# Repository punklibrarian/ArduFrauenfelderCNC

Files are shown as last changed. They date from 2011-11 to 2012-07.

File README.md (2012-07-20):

ArduFrauenfelderCNC
=============================
Copyright 2011 Design Tech Industries (DTI)  & Tamworth Hackerspace

DTI email: <the.righteous.avengers@gmail.com> |
THS: <http://tamworthhackerspace.org> |
Google Group: <https://groups.google.com/group/tamworth-hackerspace>

The ArduFrauenfelderCNC is a CNC mill run by an Arduino compatible custom board with 
stepper motor drivers, running grbl.

Board Features:

 * ATmega328 & ATmega32U4 MCU
 * Power LED & Reset switch
 * Populated pins for FTDI breakout board
 * SparkFun EasyDriver v4.4
 * Open Source; OSHW compliant
 * Design files freely available

Mill features:

 * Designed using free tools
 * Simple construction methods
 * Design files freely available

In this repository you will find the gerber files, project (.pro), board (.brd) and schematic (.sch), 
along with a grbl file configured specifically for the board.

**At the moment the files you find here are in the process of development and as such are not 
production ready. It is an ongoing endeavour to create the board and mill satisfactorily. If you can 
help in this regard please contact me, as well as if you find something that needs correction**

**The only files that can be manufactured are those of the ArduFrauenfelderCNC 1.0 - Arduino Pro Micro Edition. 
It should be a fully functional design. As on 20/07/2012 still untested.**

INSIDE THIS REPOSITORY
----------------------
The 'docs' folder within this repository includes a handy copy of the schematic in PNG format and images 
of the pcb/mill, along with assembly documentation.

The 'mill' folder within this repository has design files for the physical mill and documentation 
for it's construction. It has 'sketchup_exported_faces', 'sketchup_models' and 'laser_cutting' folders.
**For license information refer to the attached README.md file in the 'mill' folder**

The 'controller' folder within this repository has all the files needed to create the controller board. 
It has folders for the specific MCU used, 'ATmega328', 'ATmega32U4' (inside these folders are 'EAGLE', 'eagleUp', 
'KiCad' and 'gerbers' folders).

**For license information refer to the attached README.md file in the 'controller' folder**

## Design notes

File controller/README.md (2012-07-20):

ArduFrauenfelderCNC >> Controller Board
=======================================
Copyright 2012 Design Tech Industries (DTI)  & Tamworth Hackerspace

In the 'controller' folder of this repository you can find the design files for the CNC controller board in an ATmega328 
and ATmega32U4 variety. You will find project files in EAGLE and KiCad formats, as well as completed gerber files for the 
board ready to be sent to BatchPCB and OSH Park, which are the the services I designed this board to use, for manufacture.

I have also added eagleUp (http://eagleup.wordpress.com) files as well as a SKP of the resulting conversion 
(minus parts as there aren't any at the moment).

You will also find a customised version of Grbl in the form of a .HEX file. Later versions of the controller 
board will use rStep and be based on the ATmega644p MCU (I am also looking at using an mbed and http://smoothieware.org).

INSTALLATION
------------
**EAGLE**
The design is saved as an EAGLE project. EAGLE PCB design software is available from www.cadsoftusa.com 
free for non-commercial use and can be installed on Windows and Mac, with Linux support through WINE. 
To use this project download it and place the directory containing these files into the "eagle" directory 
on your computer. Then open EAGLE and navigate to Projects -> eagle -> ArduFrauenfelderCNC.

**KiCad**
KiCad EDA Suite is an Open Source alternative to EAGLE. It is available on Windows and Linux and can be installed 
on Mac. It is available from http://kicad.sourceforge.net and works in a similar way to EAGLE. You will find project 
files for KiCad in the aptly named folder in this repository. To use this project download it and place the directory 
containing these files into a folder of your choice. Then open KiCad and navigate to File -> Open -> 
'FOLDER_OF_YOUR_CHOICE' -> ArduFrauenfelderCNC.pro

You will also find a manual in the 'docs' folder for the assembly of the controller board, with colour photos and diagrams. 
**Documentation is separately licensed. See LICENSE section below**

DISTRIBUTION
------------
The specific terms of distribution of this project are governed by the license referenced below.

LICENSE
-------
> CONTROLLER BOARD
> ----------------
> This work is licensed under the Creative Commons Attribution-ShareAlike License.  
> 
> To view a copy of this license, visit:
> 
>   http://creativecommons.org/licenses/by-sa/3.0/  
>   http://creativecommons.org/licenses/by-sa/3.0/legalcode
> 
> or send a letter to
> 
>   Creative Commons  
>   171 Second Street, Suite 300  
>   San Francisco  
>   California, 94105  
>   USA

> DOCUMENTATION
> -------------
> This work is licensed under the GNU Free Documentation License Version 1.3
> 
> To view a copy of this license, visit:
> 
>   http://www.gnu.org/licenses/fdl-1.3.html

The "license" folder within this repository also contains copies of the
license(s) referenced above.

CREDITS
-------
The ArduFrauenfelderCNC was designed by Jamie Johnston (jameskun89@rocketmail.com) 
based on previous work by the Arduino team (www.arduino.cc/playground/Main/People) 
which includes:

 * Massimo Banzi
 * David Cuartielles
 * Tom Igoe
 * Gianluca Martino
 * David A. Mellis

As well as Brian Schmalz, the creator of the EasyDriver Stepper Motor Driver (http://schmalzhaus.com/EasyDriver) 
and Sparkfun, the creator of the Arduino Pro Micro (http://www.sparkfun.com/products/11098).

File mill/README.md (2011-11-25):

ArduFrauenfelderCNC >> Mill
=============================
Copyright 2011 Design Tech Industries (DTI)  & Tamworth Hackerspace

In the 'mill' folder of this repository you will find the design files for the physical mill.
You will be able to use the 3D model of the mill and will be available in either SKP, DXF or STL 
format, most likely all three. You can find the SketchUp models in the 'sketchup_models' folder.

The physical mill is being designed to be manufactured by Ponoko (http://ponoko.com) and as such 
the actual production files for the mill will be made available in SVG and EPS formats. You will 
find the files needed in the 'laser cutting' folder. You will also find the faces exported from 
SketchUp, which are used to create the templates in the 'laser cutting' folder, in the 
'sketchup_exported_faces' folder.

**The SKP, SVG and EPS files currently in this repository are, like the controller board, in 
beta versioning and as such are not ready for actual production. They are merely here for public 
critique, i.e: If you see something wrong, or you think I could be doing something better, then let 
me know.**

You will also find a manual in the 'docs' folder for the assembly of the mill, with colour photos and diagrams. 
**Documentation is separately licensed. See LICENSE section below**

DISTRIBUTION
------------
The specific terms of distribution of this project are governed by the license referenced below.

LICENSE
-------
> MILL
> ----
> This work is licensed under the Creative Commons Attribution-ShareAlike License 3.0  
> 
> To view a copy of this license, visit:
> 
>   http://creativecommons.org/licenses/by-sa/3.0/  
>   http://creativecommons.org/licenses/by-sa/3.0/legalcode
> 
> or send a letter to
> 
>   Creative Commons  
>   171 Second Street, Suite 300  
>   San Francisco  
>   California, 94105  
>   USA

The "license" folder within this repository also contains copies of the
license(s) referenced above.

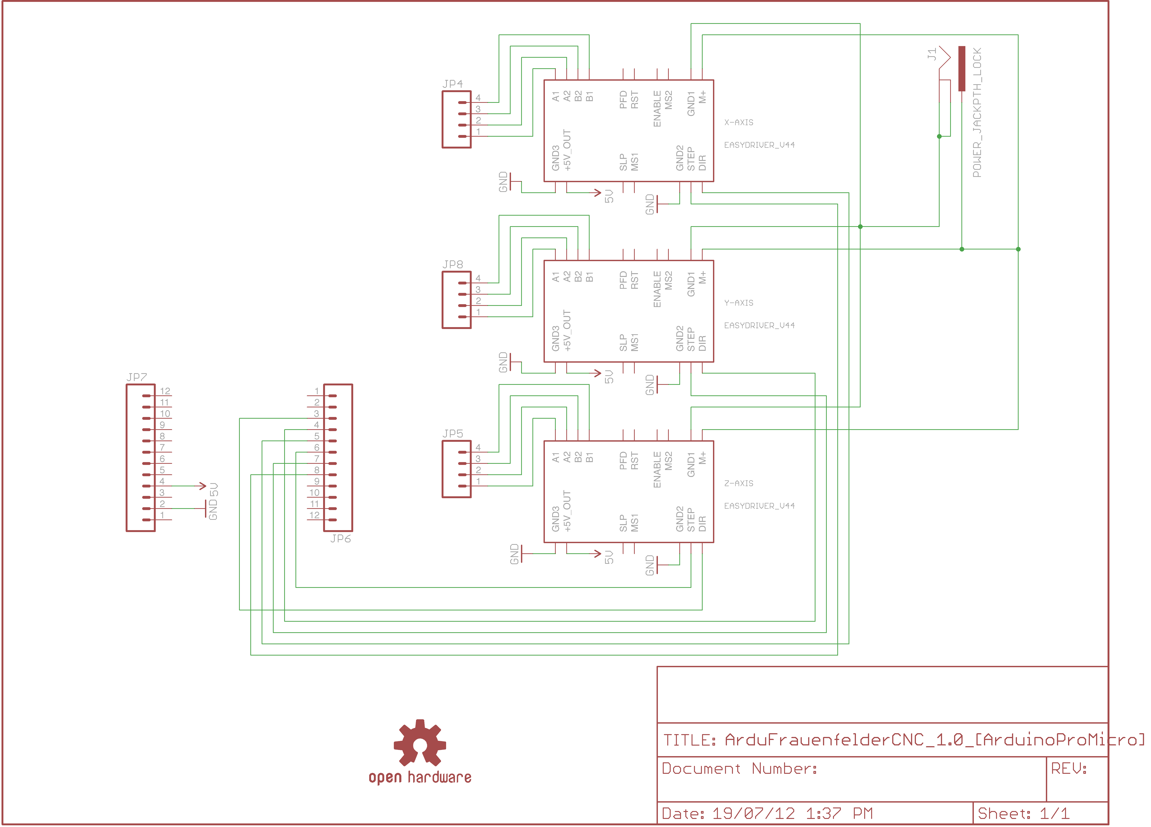
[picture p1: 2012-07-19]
docs/ArduFrauenfelderCNC_1.0_[ArduinoProMicro]_schematic.png

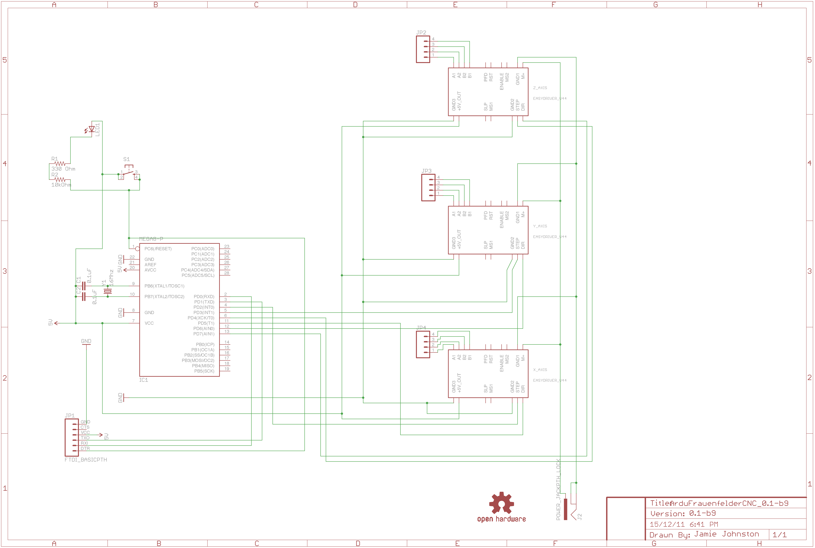
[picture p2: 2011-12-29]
docs/ArduFrauenfelderCNC_0.1-b9_schematic.png

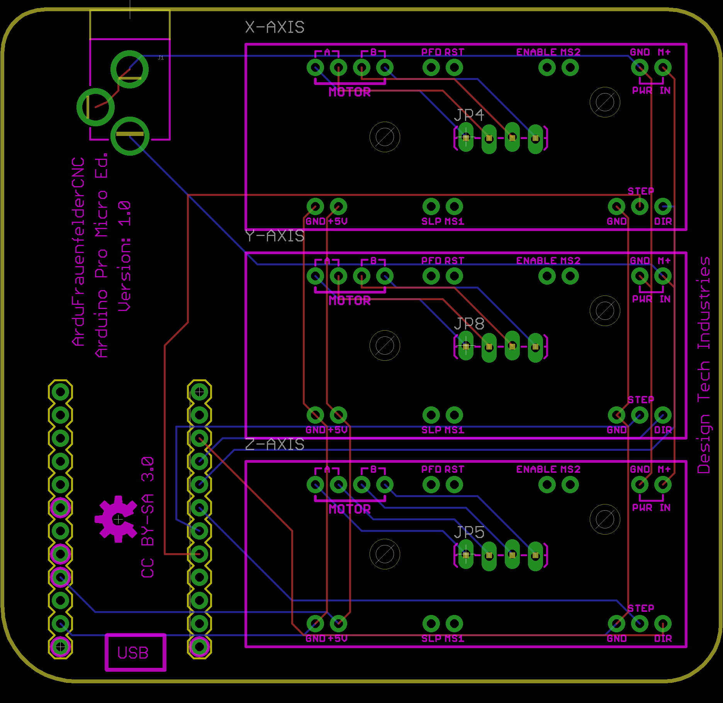
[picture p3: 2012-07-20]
docs/ArduFrauenfelderCNC_1.0_[ArduinoProMicro]_board_image.png

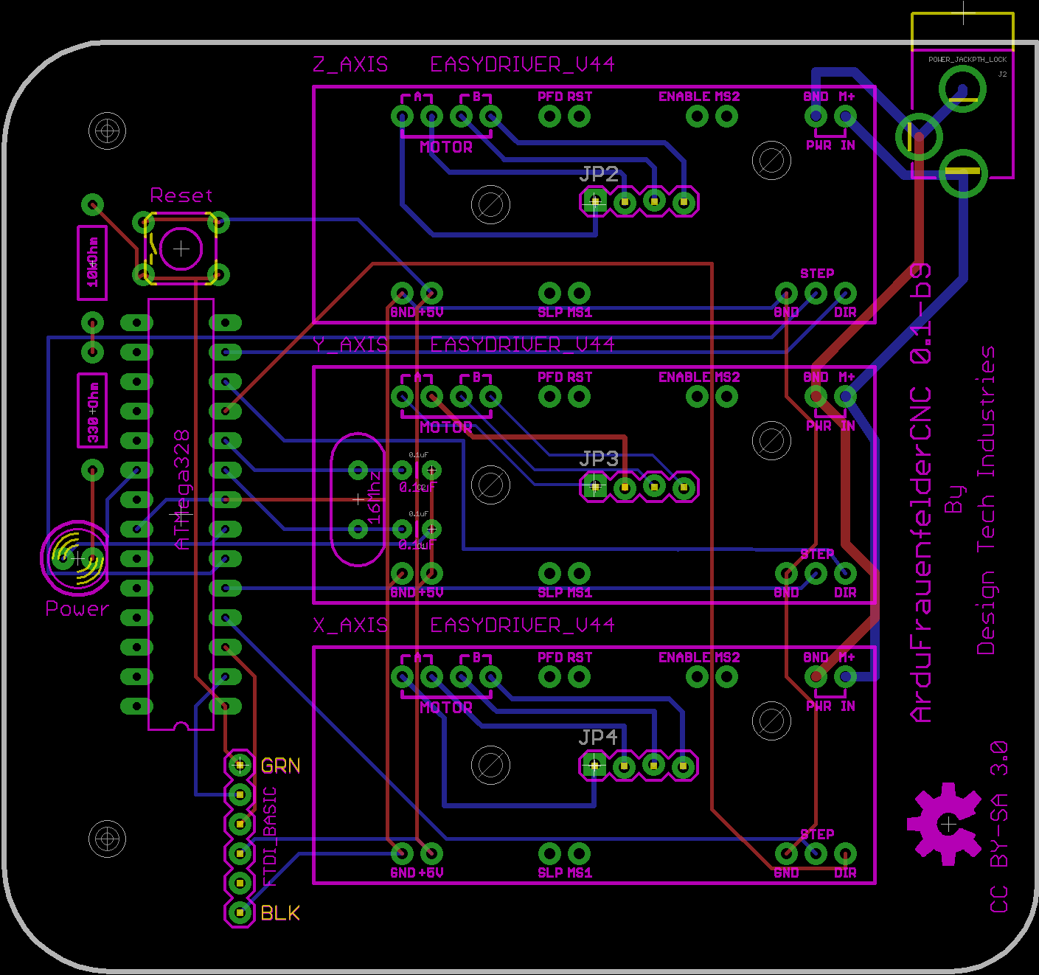
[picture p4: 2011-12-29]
docs/ArduFrauenfelderCNC_0.1-b9_board_image.png

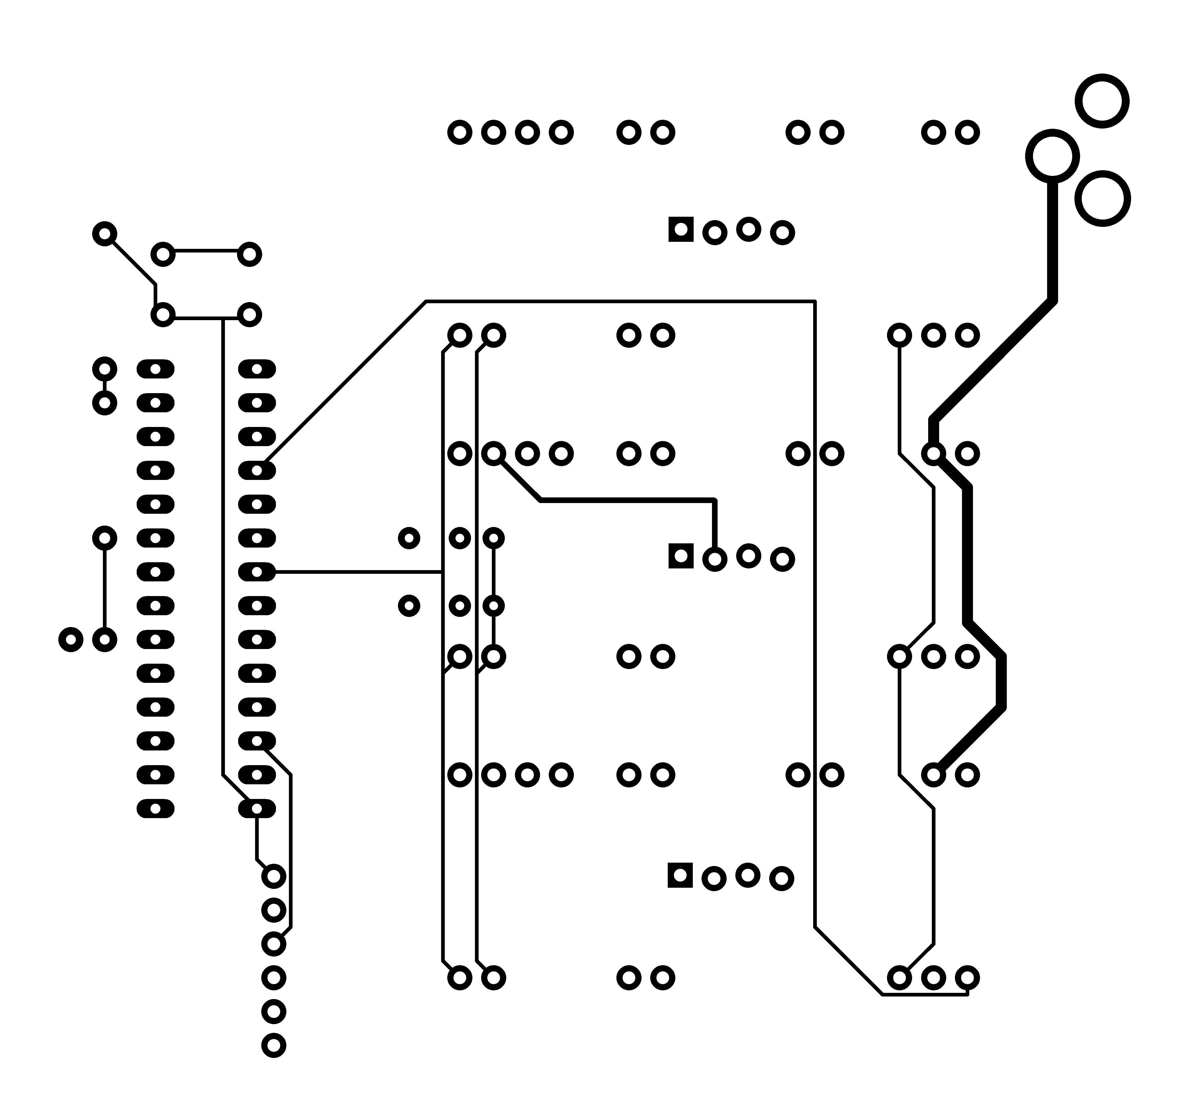
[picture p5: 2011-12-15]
controller/ATmega328/EAGLE/ArduFrauenfelderCNC/eagleUp/eagleUp_ArduFrauenfelderCNC_0.1-b9_top.png

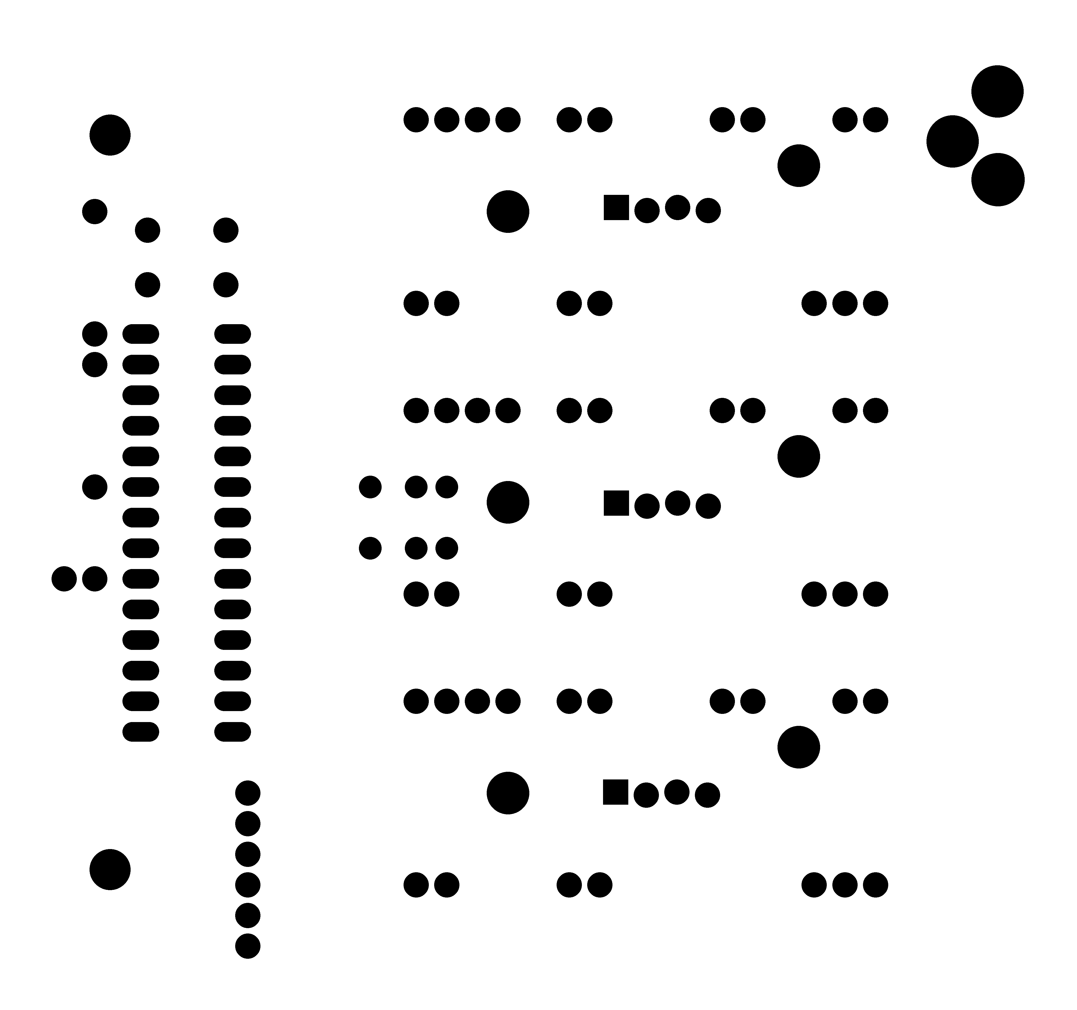
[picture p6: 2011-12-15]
controller/ATmega328/EAGLE/ArduFrauenfelderCNC/eagleUp/eagleUp_ArduFrauenfelderCNC_0.1-b9_bottom_mask.png

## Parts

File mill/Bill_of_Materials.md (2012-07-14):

Material List
=============

This is a list of the materials you will need to construct the physical mill (that is, materials other than the materials 
gained from fab houses). 

I have included, in most cases, places these materials can be acquired from (most will be where I 
initially bought my supplies from).

Linear Motion
-------------

* Linear Bearings - 10 mm - http://www.ebay.com.au/itm/290562133939?ssPageName=STRK:MESINDXX:IT&_trksid=p3984.m1436.l2649
* Linear Rail - 10 mm - http://www.ebay.com.au/itm/300676109305?ssPageName=STRK:MESINDXX:IT&_trksid=p3984.m1436.l2649
* Rail Support - http://www.ebay.com.au/itm/290710891416?ssPageName=STRK:MESINDXX:IT&_trksid=p3984.m1436.l2649

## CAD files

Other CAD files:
controller/ATmega328/EAGLE/ArduFrauenfelderCNC/eagleUp/eagleUp_AFCNC_0.1b9.skp
mill/3d_printing/SKP_models/ArduFrauenfelderCNC_Z-axis_linear_bearing_manifold.skp
mill/3d_printing/SKP_models/ArduFrauenfelderCNC_controller-board+holder.skp
mill/sketchup_models/ArduFrauenfelderCNC_Zaxis_drill_platform[experimental].skp
mill/sketchup_models/ArduFrauenfelderCNC_base[split-ends].skp
mill/sketchup_models/ArduFrauenfelderCNC_base[split-ends]_gantry_experimental-Zaxis_controller-board-holder_Z-axis-linear-bearing-manifold.skp
mill/sketchup_models/ArduFrauenfelderCNC_gantry.skp

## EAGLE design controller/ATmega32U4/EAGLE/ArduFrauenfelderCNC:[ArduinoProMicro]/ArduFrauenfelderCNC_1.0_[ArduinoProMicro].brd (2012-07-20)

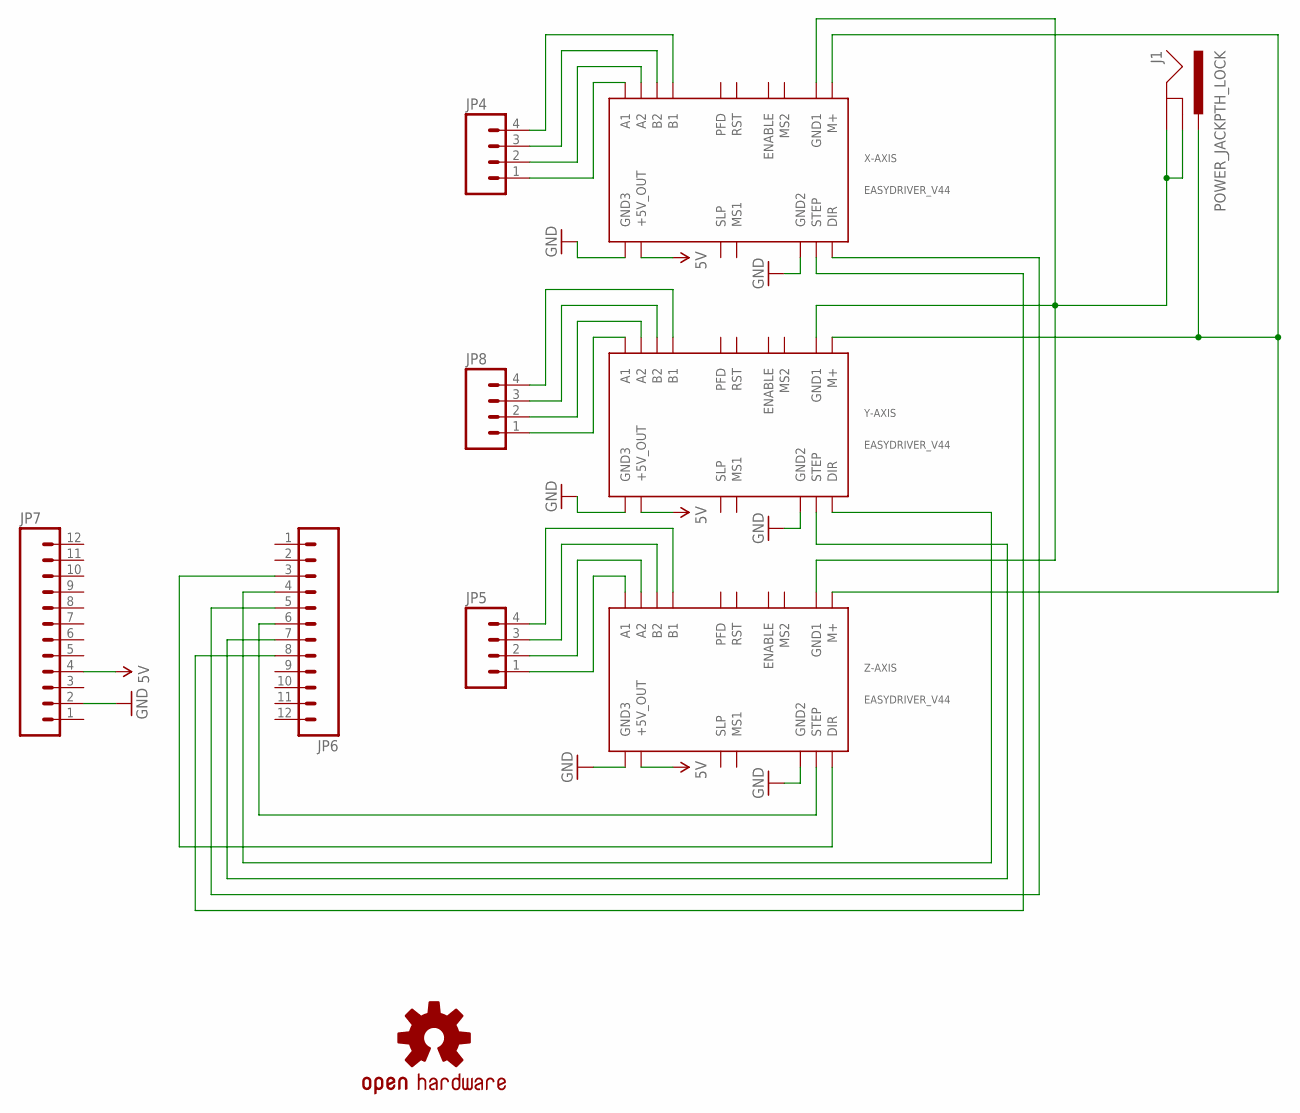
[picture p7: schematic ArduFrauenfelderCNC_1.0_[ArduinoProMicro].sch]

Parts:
J1: POWER_JACKPTH_LOCK; POWER_JACK_PTH_LOCK
JP4, JP5, JP8: M04LOCK_LONGPADS; 1X04_LOCK_LONGPADS
JP6, JP7: M12PTH; 1X12
U$2: OSHW-LOGOM; OSHW-LOGO-M
X-AXIS: EASYDRIVER_V44
Y-AXIS: EASYDRIVER_V44
Z-AXIS: EASYDRIVER_V44

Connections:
5V: JP7.4, X-AXIS.P$11 (+5V_OUT), Y-AXIS.P$11 (+5V_OUT), Z-AXIS.P$11 (+5V_OUT)
GND: JP7.2, X-AXIS.GND2, X-AXIS.GND3, Y-AXIS.GND2, Y-AXIS.GND3, Z-AXIS.GND2, Z-AXIS.GND3
unnamed: J1.GND, J1.GNDBREAK, X-AXIS.GND1, Y-AXIS.GND1, Z-AXIS.GND1
unnamed: JP4.1, X-AXIS.A1
unnamed: JP4.2, X-AXIS.A2
unnamed: J1.PWR, X-AXIS.M+, Y-AXIS.M+, Z-AXIS.M+
unnamed: JP4.3, X-AXIS.B2
unnamed: JP4.4, X-AXIS.B1
unnamed: JP8.1, Y-AXIS.A1
unnamed: JP8.2, Y-AXIS.A2
unnamed: JP8.3, Y-AXIS.B2
unnamed: JP8.4, Y-AXIS.B1
unnamed: JP5.1, Z-AXIS.A1
unnamed: JP5.2, Z-AXIS.A2
unnamed: JP5.3, Z-AXIS.B2
unnamed: JP5.4, Z-AXIS.B1
unnamed: JP6.8, X-AXIS.STEP
unnamed: JP6.5, X-AXIS.DIR
unnamed: JP6.7, Y-AXIS.STEP
unnamed: JP6.4, Y-AXIS.DIR
unnamed: JP6.6, Z-AXIS.STEP
unnamed: JP6.3, Z-AXIS.DIR

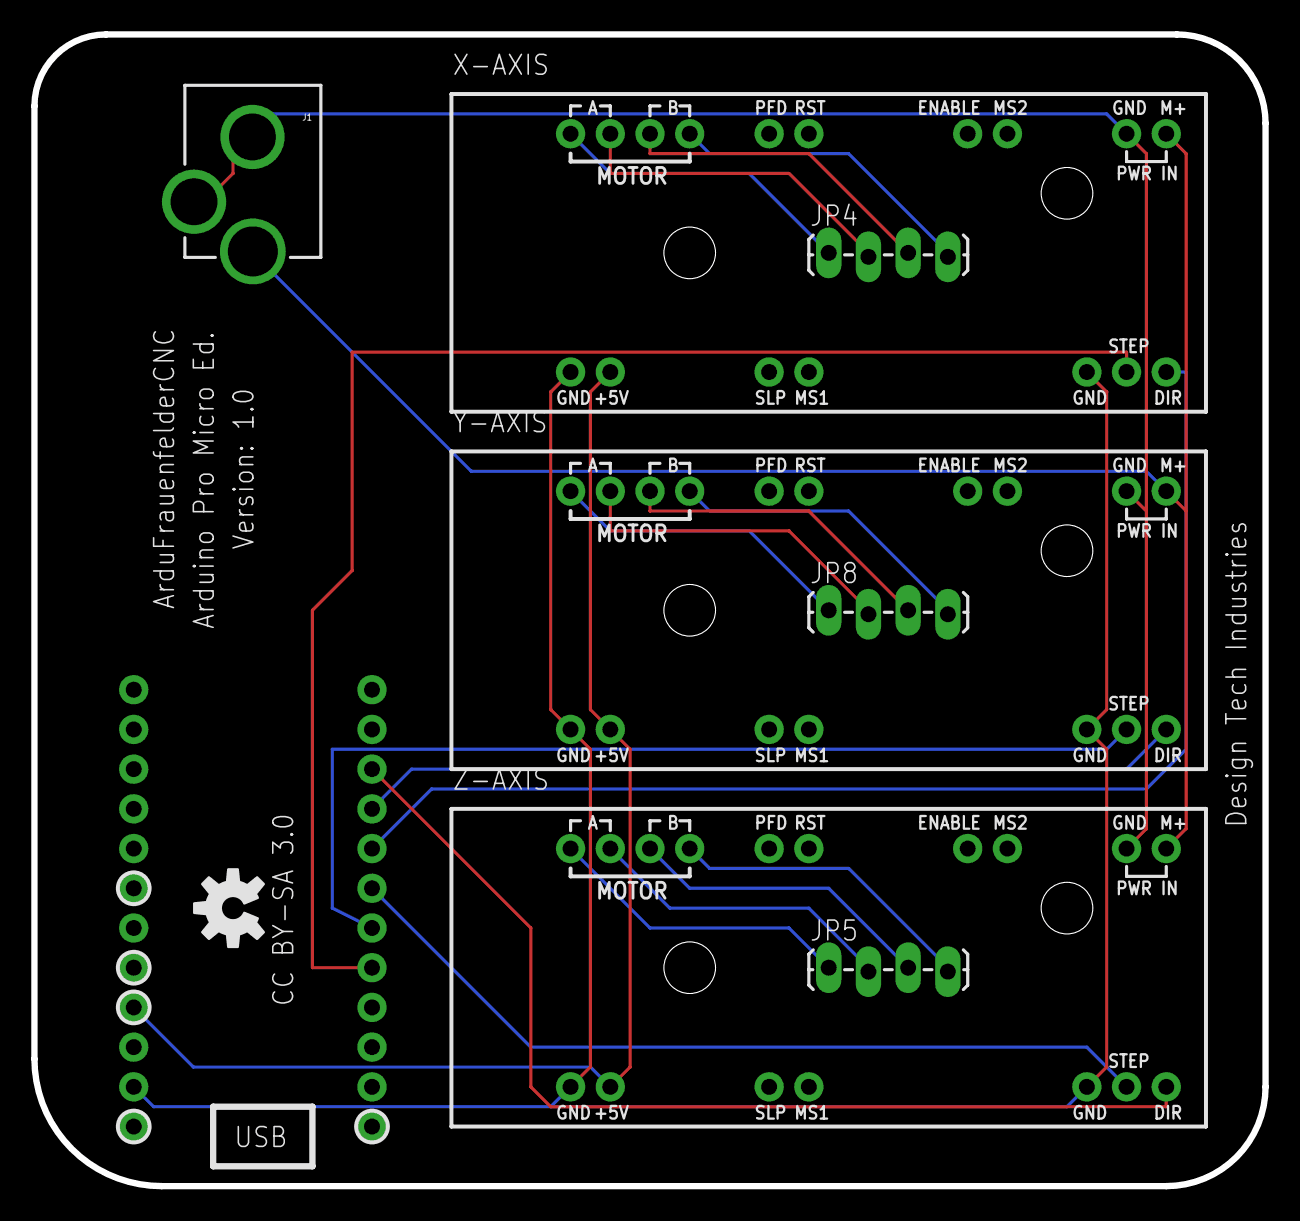
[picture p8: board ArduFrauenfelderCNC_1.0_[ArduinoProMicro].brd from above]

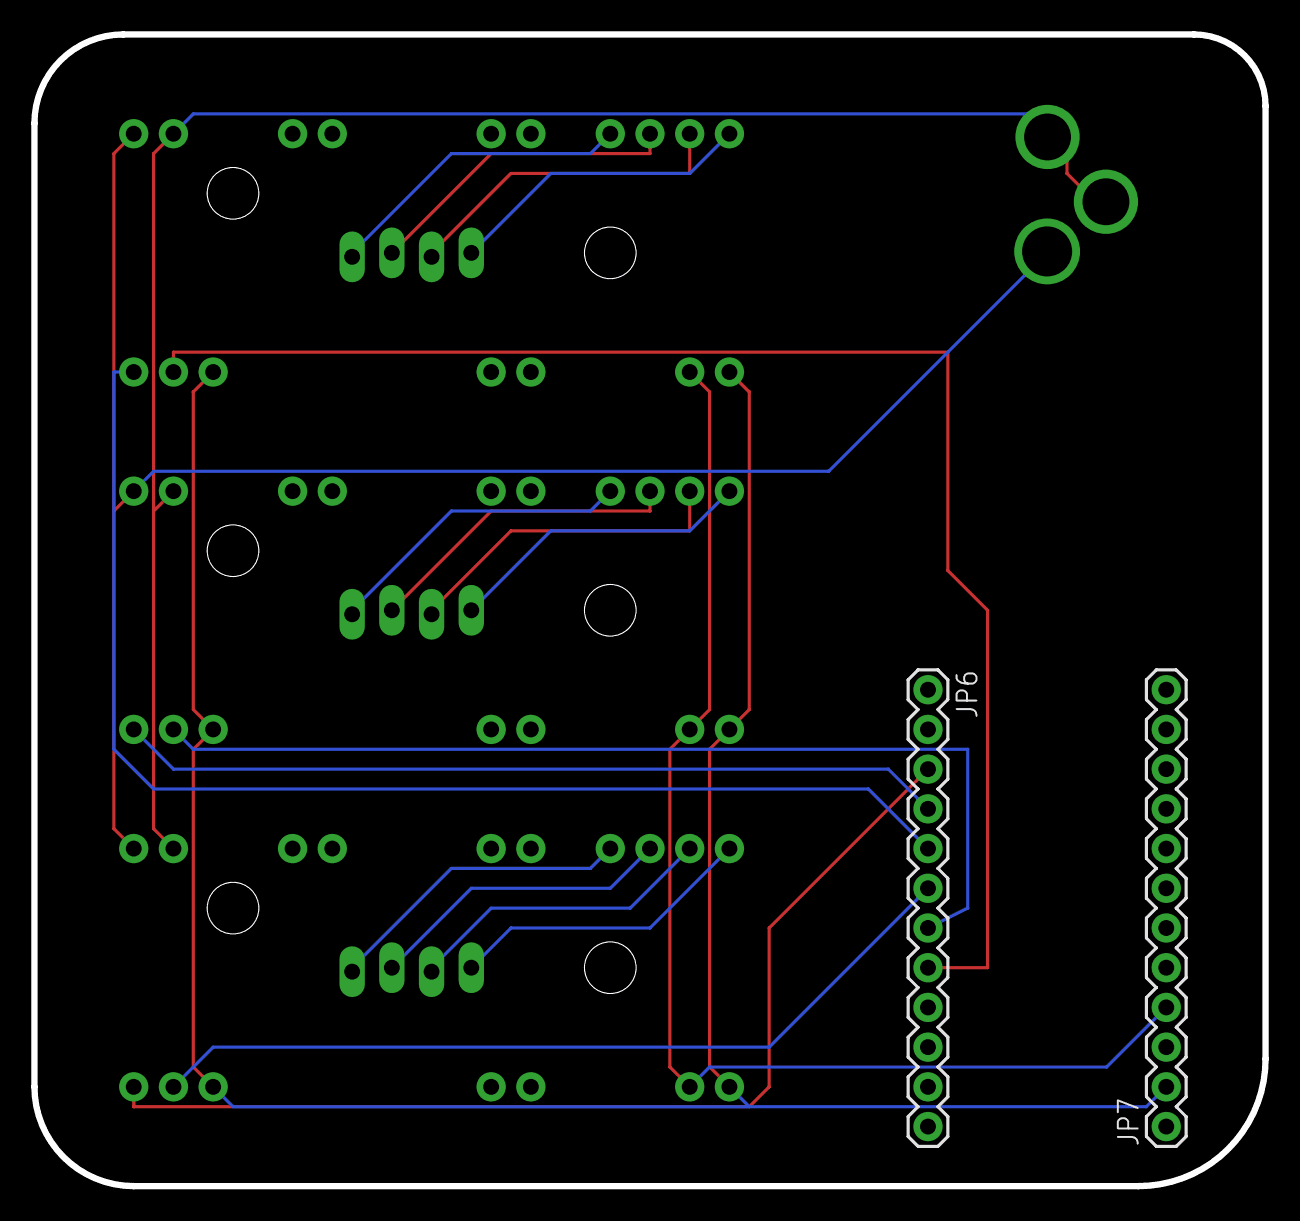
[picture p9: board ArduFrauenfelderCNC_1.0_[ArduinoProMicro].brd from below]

Board: 2 copper layers, 78.7 x 73.7 mm, 10 parts (2 on the bottom side), 22 nets.

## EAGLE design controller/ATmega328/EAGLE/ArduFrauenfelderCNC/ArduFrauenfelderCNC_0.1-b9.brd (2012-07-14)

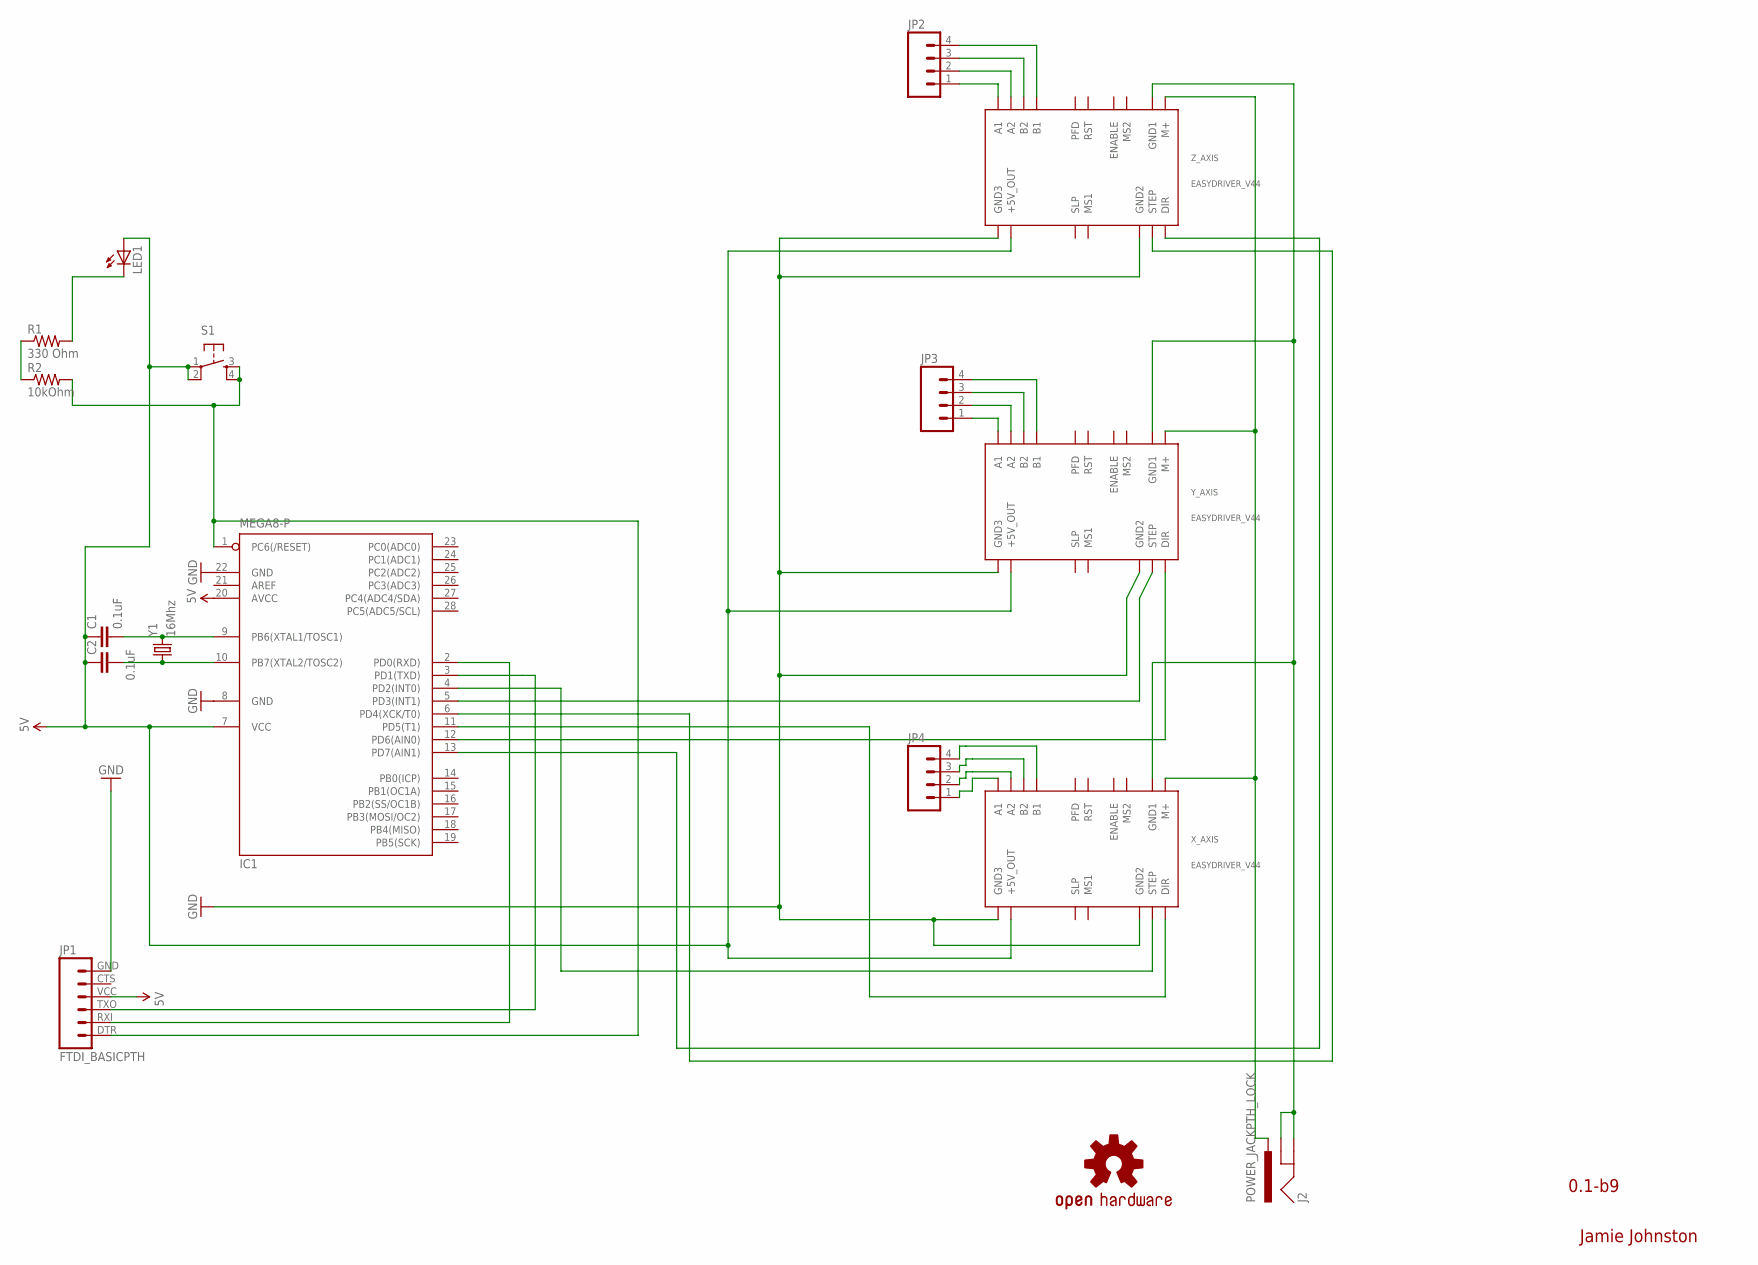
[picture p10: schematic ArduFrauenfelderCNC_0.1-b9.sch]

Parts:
C1, C2: 0.1uF; CAP-PTH-SMALL
IC1: MEGA8-P; DIL28-3
J2: POWER_JACKPTH_LOCK; POWER_JACK_PTH_LOCK
JP1: FTDI_BASICPTH; FTDI_BASIC
JP2, JP3, JP4: M04LOCK; 1X04_LOCK
LED1: LED5MM
R1: 330 Ohm; AXIAL-0.4
R2: 10kOhm; AXIAL-0.4
S1: TAC_SWITCHPTH; TACTILE-PTH
U$2: OSHW-LOGOL; OSHW-LOGO-L
X_AXIS: EASYDRIVER_V44
Y1: 16Mhz; HC49US
Y_AXIS: EASYDRIVER_V44
Z_AXIS: EASYDRIVER_V44

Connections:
5V: C1.1, C2.1, IC1.7 (VCC), IC1.20 (AVCC), JP1.VCC (4), LED1.A, S1.1, S1.2, X_AXIS.P$11 (+5V_OUT), Y_AXIS.P$11 (+5V_OUT), Z_AXIS.P$11 (+5V_OUT)
GND: IC1.8 (GND), IC1.22 (GND), JP1.GND (6), X_AXIS.GND2, X_AXIS.GND3, Y_AXIS.GND2, Y_AXIS.GND3, Z_AXIS.GND2, Z_AXIS.GND3
unnamed: C1.2, IC1.9 (PB6(XTAL1/TOSC1)), Y1.2
unnamed: C2.2, IC1.10 (PB7(XTAL2/TOSC2)), Y1.1
unnamed: IC1.5 (PD3(INT1)), Y_AXIS.STEP
unnamed: LED1.K (C), R1.P$2 (2)
unnamed: IC1.1 (PC6(/RESET)), JP1.DTR (1), R2.P$2 (2), S1.3, S1.4
unnamed: R1.P$1 (1), R2.P$1 (1)
unnamed: JP2.1, Z_AXIS.A1
unnamed: J2.PWR, X_AXIS.M+, Y_AXIS.M+, Z_AXIS.M+
unnamed: JP2.2, Z_AXIS.A2
unnamed: J2.GND, J2.GNDBREAK, X_AXIS.GND1, Y_AXIS.GND1, Z_AXIS.GND1
unnamed: IC1.3 (PD1(TXD)), JP1.TXO (3)
unnamed: IC1.2 (PD0(RXD)), JP1.RXI (2)
unnamed: IC1.12 (PD6(AIN0)), Y_AXIS.DIR
unnamed: IC1.4 (PD2(INT0)), X_AXIS.STEP
unnamed: JP2.3, Z_AXIS.B2
unnamed: IC1.11 (PD5(T1)), X_AXIS.DIR
unnamed: JP2.4, Z_AXIS.B1
unnamed: JP3.1, Y_AXIS.A1
unnamed: IC1.13 (PD7(AIN1)), Z_AXIS.DIR
unnamed: IC1.6 (PD4(XCK/T0)), Z_AXIS.STEP
unnamed: JP3.2, Y_AXIS.A2
unnamed: JP3.3, Y_AXIS.B2
unnamed: JP3.4, Y_AXIS.B1
unnamed: JP4.1, X_AXIS.A1
unnamed: JP4.2, X_AXIS.A2
unnamed: JP4.3, X_AXIS.B2
unnamed: JP4.4, X_AXIS.B1

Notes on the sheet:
Jamie Johnston
0.1-b9

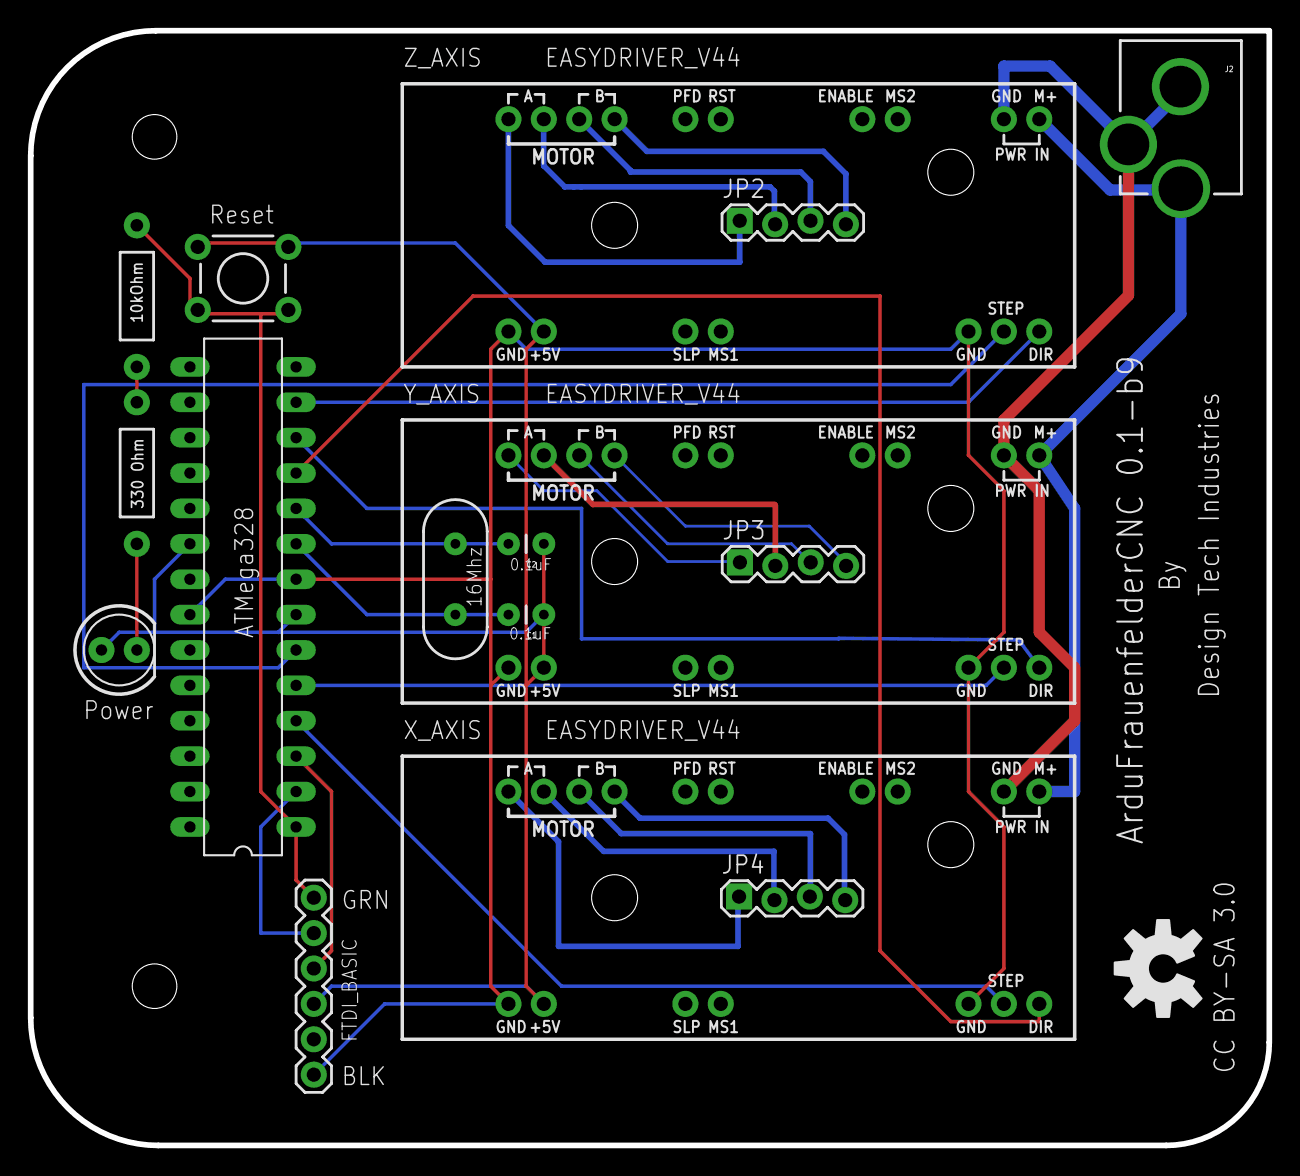
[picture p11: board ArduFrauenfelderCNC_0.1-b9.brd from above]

Board: 2 copper layers, 88.9 x 80.0 mm, 17 parts (0 on the bottom side), 29 nets.

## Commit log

2011-11-18 Initial Commit -Jamie
    [ArduFrauenfelderCNC.brd, ArduFrauenfelderCNC.sch]
2011-11-18 Changed file/folder structure so as to aid in program identification.
    [ArduFrauenfelderCNC.brd, ArduFrauenfelderCNC.sch]
2011-11-19 Added Open Hardware symbol, board name, board version, board license (CC BY-SA 3.0), drill hole markers and reference to designing parties (DTI and THS).
    [ArduFrauenfelderCNC.brd]
2011-11-19 Found GND pins connected to +5v power pins. Rectified and traces are now more organised (only one jumper wire needed). Updated version to 0.1-b3.
    [ArduFrauenfelderCNC.brd, ArduFrauenfelderCNC.sch]
2011-11-19 Conversion of EAGLE schematic to KiCad format (untested), using eagle2kicad.ulp V1.1
    [ArduFrauenfelderCNC.sch]
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2011-11-19 Added version detail to schematic, as well as creators name and OSHW logo.
    [ArduFrauenfelderCNC.sch]
2011-11-19 Slight edit: added extra OSHW logo to board due to addition of logo to schematic.
    [ArduFrauenfelderCNC.brd]
2011-11-19 Update of schematic for KiCad (untested). Converted using eagle2kicad.ulp V1.1 and includes an initial commit of the .lib and .pro files.
    [ArduFrauenfelderCNC.sch]
2011-11-19 Minor edit: repositioned second OSHW logo, added GRN & BLK to tPlace layer and changed tDocu layer colour to yellow.
    [ArduFrauenfelderCNC.brd]
2011-11-20 Creation and initial commit of prototype Gerber files using SparkFun's CAM file (sfe-gerb274x.cam). Included are the seven files needed by fab houses and a tar.gz copy of files for ease of use.
    [ArduFrauenfelderCNC.GBL, ArduFrauenfelderCNC.GBO, ArduFrauenfelderCNC.GBS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]
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2011-11-20 Re-commit of previously named 'Gerber' folder. Change of name to 'gerber'.
    [ArduFrauenfelderCNC.GBL, ArduFrauenfelderCNC.GBO, ArduFrauenfelderCNC.GBS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]
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2011-11-21 Incorrect Drill file found. Replaced with correct file and recompressed to tar.gz archive.
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2011-11-22 Moved PCB design related files to the 'controller' folder.
    [ArduFrauenfelderCNC.brd, ArduFrauenfelderCNC.sch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]
2011-11-23 Initial commit of mill base and gantry in .SKP format.
    [ArduFrauenfelderCNC_base_and_gantry.skp]
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2011-11-24 Added new gantry design to SKP file and new SVG export, as well as made models proper 3D versions. Deleted SVG and EPS templates.
    [ArduFrauenfelderCNC_base_and_gantry.skp]
2011-11-24 Moved SketchUp models to own folder and added separated models of the base and gantry.
    [ArduFrauenfelderCNC_base.skp, ArduFrauenfelderCNC_base_and_gantry.skp, ArduFrauenfelderCNC_gantry.skp]
2011-11-24 Changed end plate design of mill base to allow for Ponoko laser cutting, as well as changing the width of the gantry [I was made aware that it was too wide to fit into the base].
    [ArduFrauenfelderCNC_base[split-ends].skp, ArduFrauenfelderCNC_base[split-ends]_and_gantry.skp, ArduFrauenfelderCNC_base_and_gantry.skp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]
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2011-11-25 Change made to silkscreen layer to include component names and drill hole placement altered.
    [ArduFrauenfelderCNC.brd, ArduFrauenfelderCNC.sch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]
2011-11-25 Revert "Change made to silkscreen layer to include component names and drill hole placement altered."
    This reverts commit 92fa80944d13c01f441f73ab6e0e381a67eb5132.
    [ArduFrauenfelderCNC.brd, ArduFrauenfelderCNC.sch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]
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2011-11-26 New board version with errors corrected (0.1-b3 -> 0.1-b6). New naming scheme initiated.
    [ArduFrauenfelderCNC_0.1-b6.brd, ArduFrauenfelderCNC_0.1-b6.sch]
2011-11-26 Initial commit of eagleUp files and SKP board file.
    [eagleUp_AFCNC_0.1b6_[no-parts].skp]
2011-11-26 New part included, Z-axis and drill platform [experimental]
    [ArduFrauenfelderCNC_Zaxis_drill_platform[experimental].skp, ArduFrauenfelderCNC_base[split-ends]_experimental-Zaxis_and_gantry.skp]
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2011-11-27 Updated for new board design. As well as having some components placed, including EasyDriver boards.
    [eagleUp_AFCNC_0.1b6.skp]
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2011-12-15 Updated design to 0.1-b9 [added three four-pin screw terminals for stepper motor connection].
    [ArduFrauenfelderCNC_0.1-b6.brd, ArduFrauenfelderCNC_0.1-b6.sch, ArduFrauenfelderCNC_0.1-b8.brd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]
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2012-07-14 A general update of modified files [Includes new gantry and Z-axis design]
    [ArduFrauenfelderCNC_0.1-b9.brd, ArduFrauenfelderCNC_0.1-b9.sch, ArduFrauenfelderCNC_Zaxis_drill_platform[experimental].skp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]
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2012-07-14 Update to the gantry model to include linear bearing guides and manifold.
    [ArduFrauenfelderCNC_base[split-ends]_experimental-Zaxis_and_gantry.skp, ArduFrauenfelderCNC_gantry.skp]
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2012-07-14 Addition of 3D printed parts (Z-axis bearing housing), as well as 3D model and .dae of controller board holder. Included Ponoko laser cutting templates for reference.
    [ArduFrauenfelderCNC_base[split-ends]_gantry_experimental-Zaxis_and__controller-board+holder.skp, ArduFrauenfelderCNC_base[split-ends]_gantry_experimental-Zaxis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]
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2012-07-19 Restructure of folders. Initial commit of additional board design. Update to KiCAD files. Renamed 'DorkbotPDX' to the new 'OSH Park'.
    I have moved files from a general folder structure to a board specific
    structure, i.e: 'ArduFrauenfelderCNC' and
    'ArduFrauenfelderCNC_[ArduinoProMicro]'.
    The new controller board uses an Arduino Pro Micro, taking away the
    need for a FTDI adaptor and smartening things up. I will of course
    continue developing the cheaper on-board Arduino version but this is a
    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
    [ArduFrauenfelderCNC_0.1-b9.brd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]
2012-07-19 Change made to complete model .skp file to include new controller board holder, as well as schematic & board images.
    [ArduFrauenfelderCNC_base[split-ends]_gantry_experimental-Zaxis_controller-board-holder_Z-axis-linear-bearing-manifold.skp]
2012-07-20 Changed folder structure to be MCU specific, moving designs into 'ATmega328' and 'ATmega32U4' folders. Updated REAME.md's to reflect changes.
    [ArduFrauenfelderCNC_0.1-b9.brd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]
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
